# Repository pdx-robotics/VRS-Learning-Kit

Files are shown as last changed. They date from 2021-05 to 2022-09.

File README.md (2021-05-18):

This is a learning kit developed by Michael Nguyen. It is intended to train Viking Robotics
Society (VRS) students in the mechanical and electrical assembly of robots. This project was initially
Michael Nguyen's first entry to his professional portfolio, but the president at the time, Anthony
Bruno, suggested that it should be utilized as a learning kit for VRS students as well.
Video footage of the VRS Learning Kit in action is found in this link: https://www.youtube.com/watch?v=XiWULx6cqs4
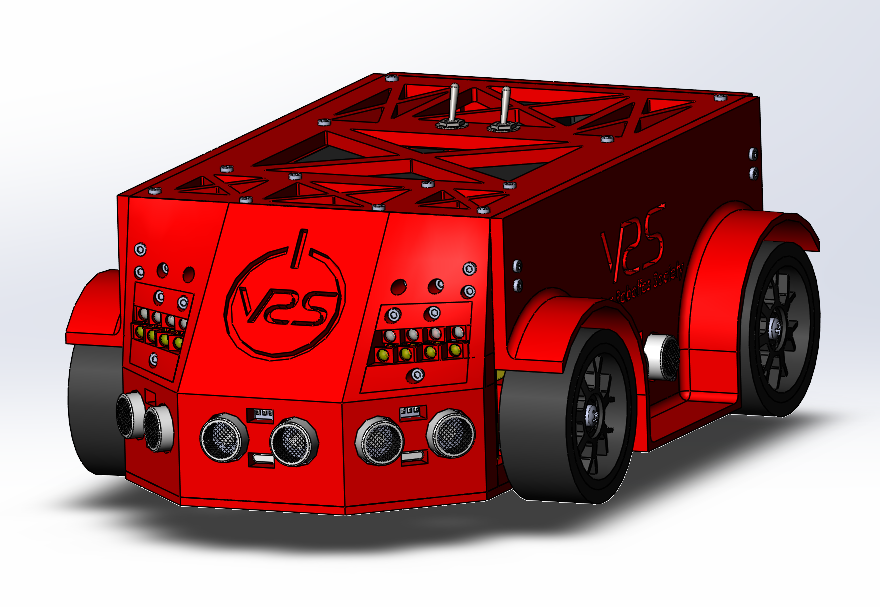
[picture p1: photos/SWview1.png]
 
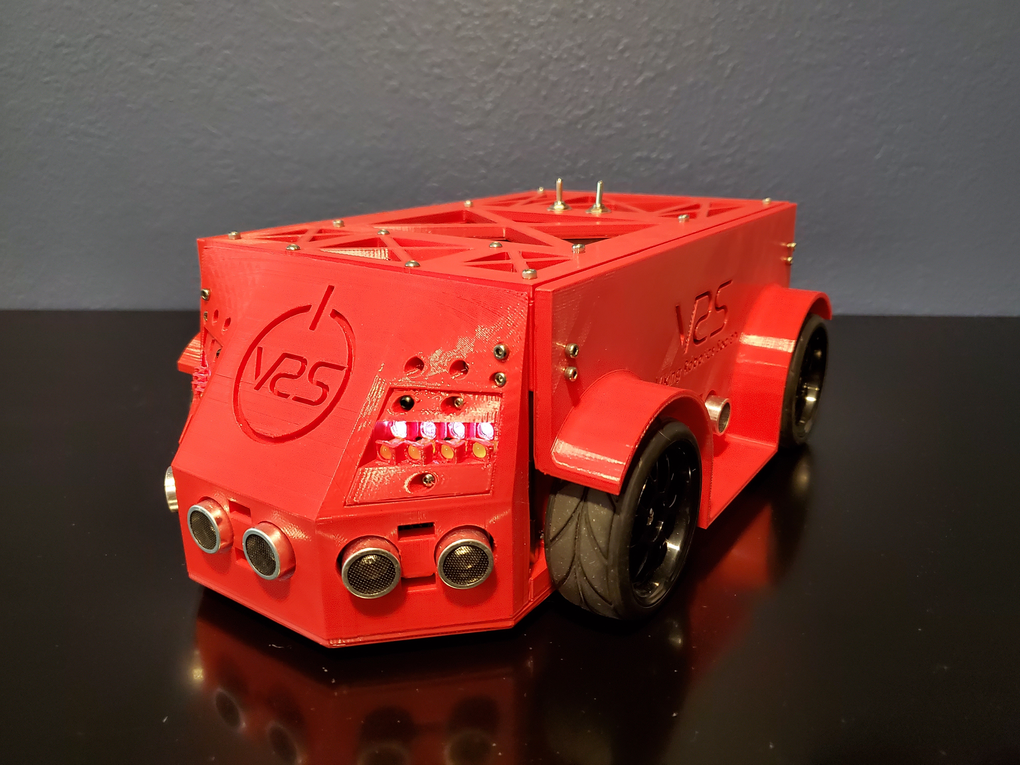
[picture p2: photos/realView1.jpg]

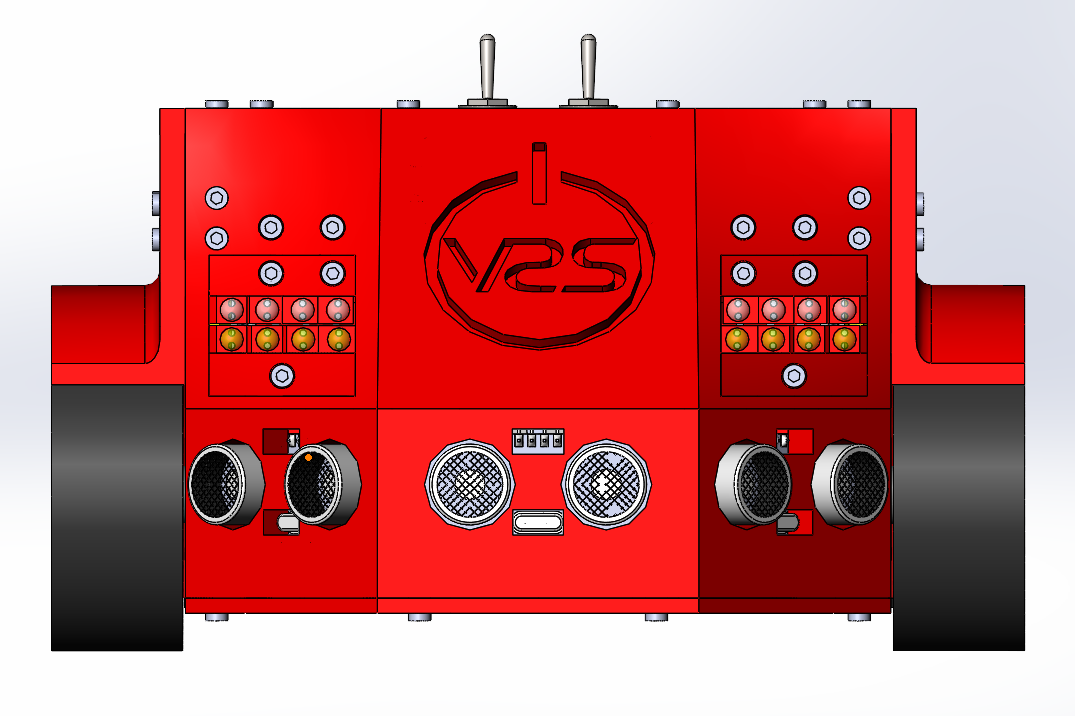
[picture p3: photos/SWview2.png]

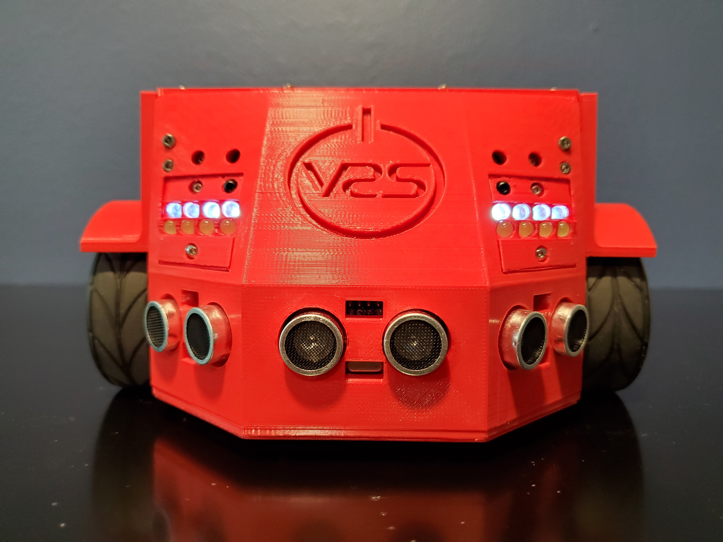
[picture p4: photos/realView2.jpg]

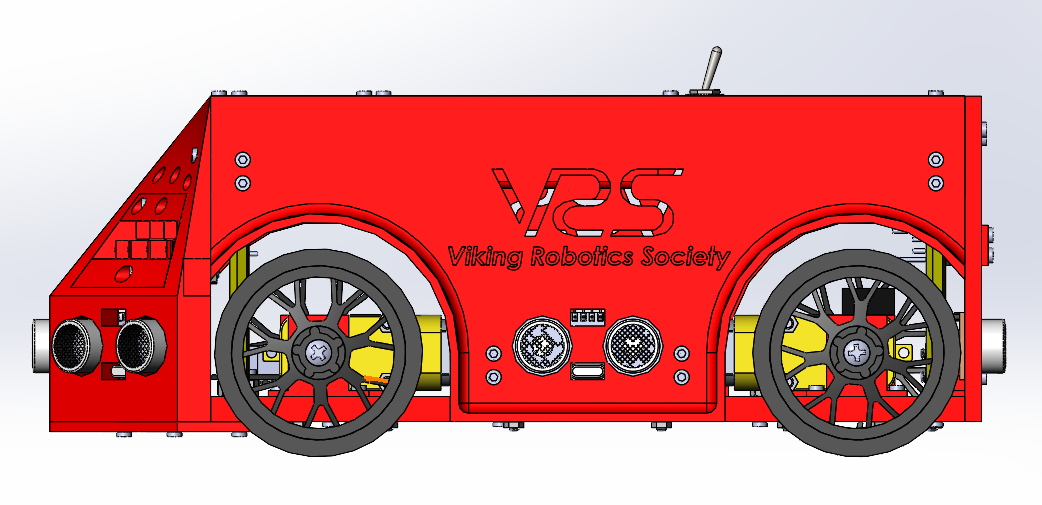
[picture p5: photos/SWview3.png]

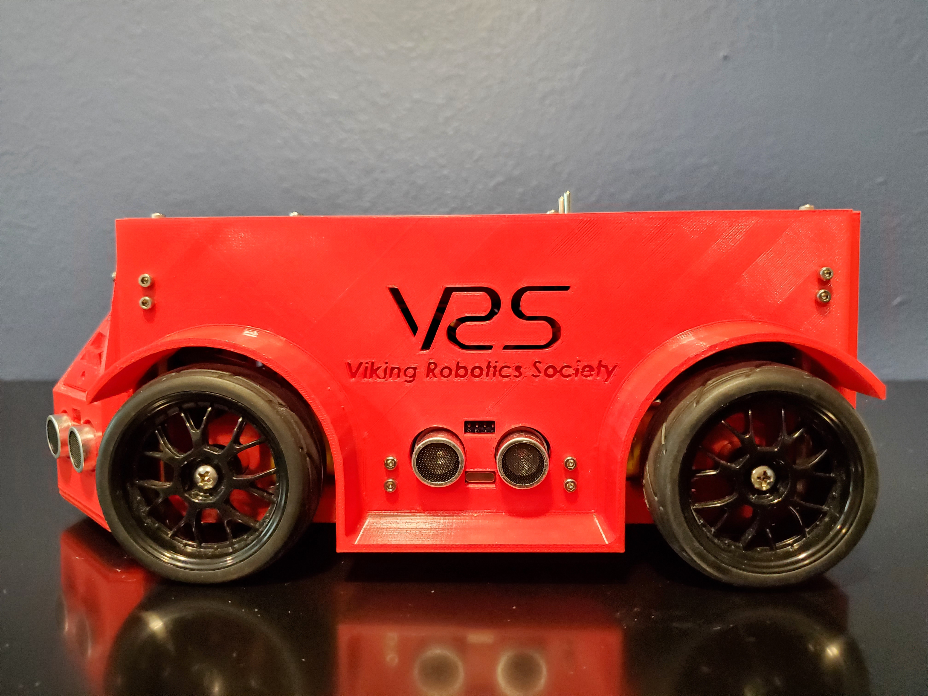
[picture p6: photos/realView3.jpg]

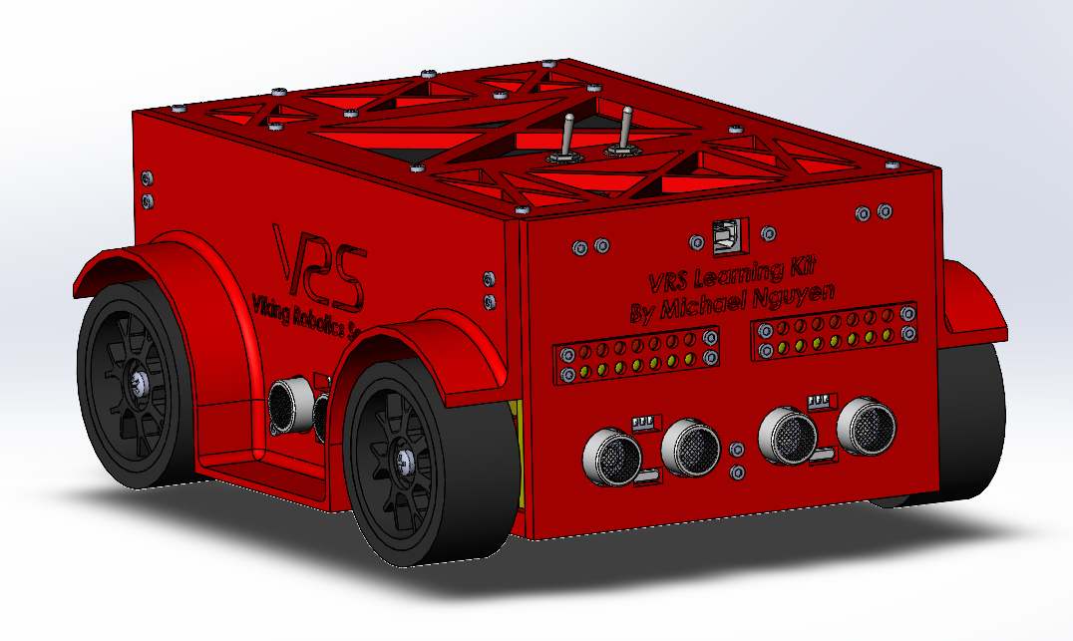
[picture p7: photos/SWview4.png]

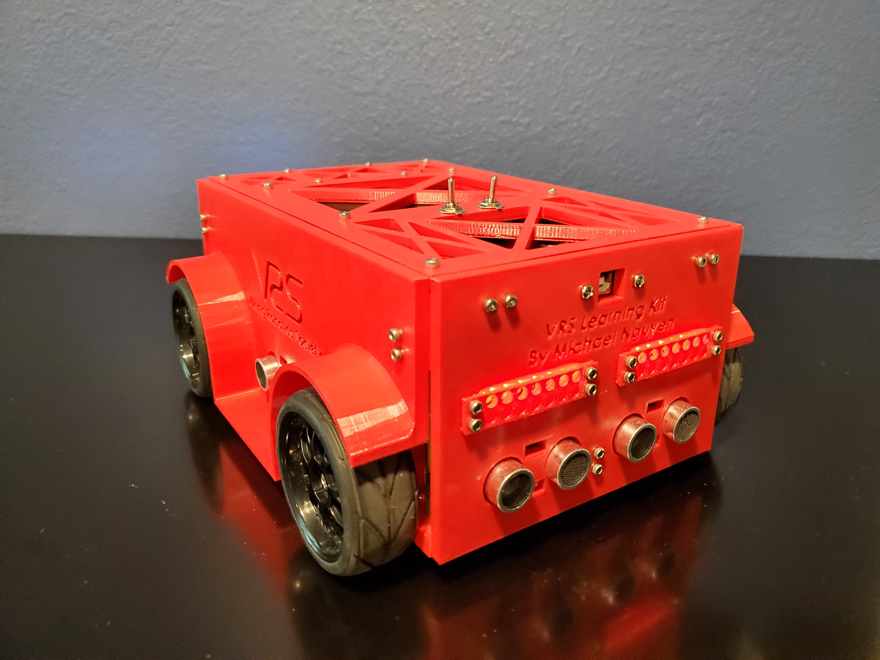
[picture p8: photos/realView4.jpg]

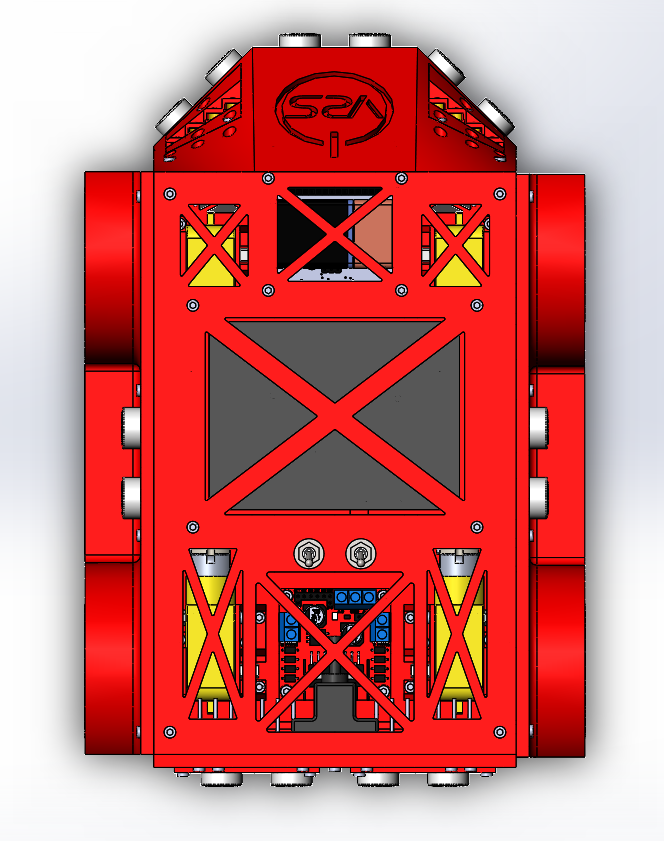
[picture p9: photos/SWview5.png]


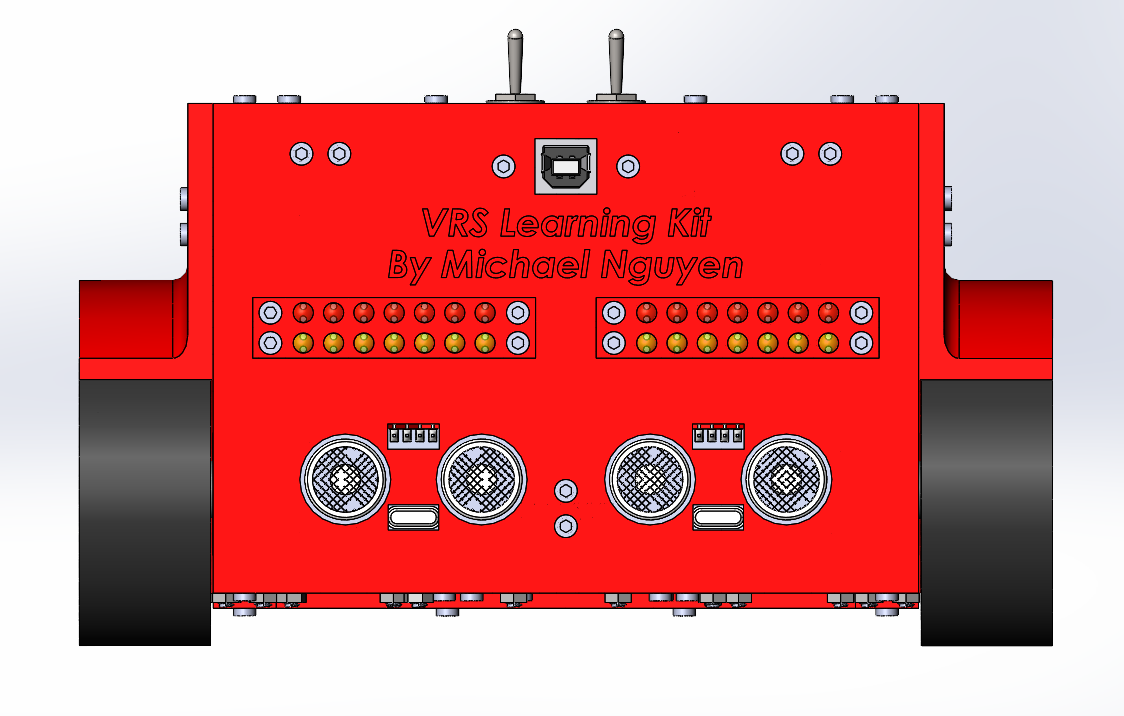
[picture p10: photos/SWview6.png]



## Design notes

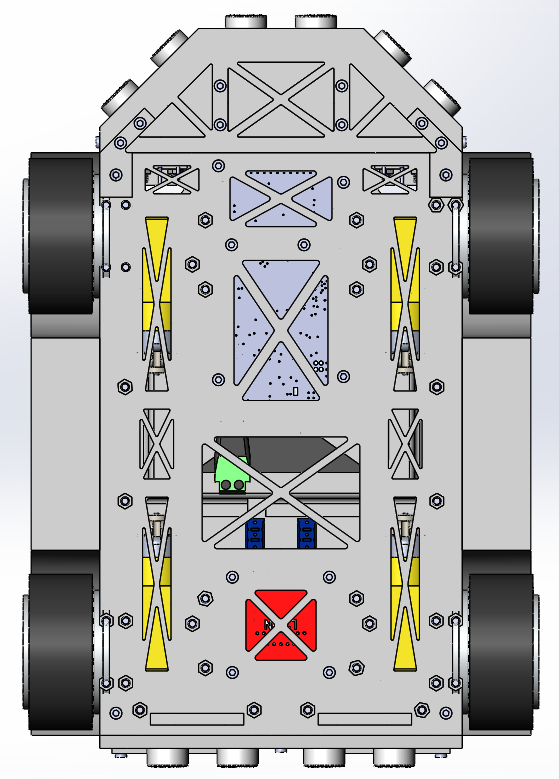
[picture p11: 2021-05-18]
photos/basicView4.png

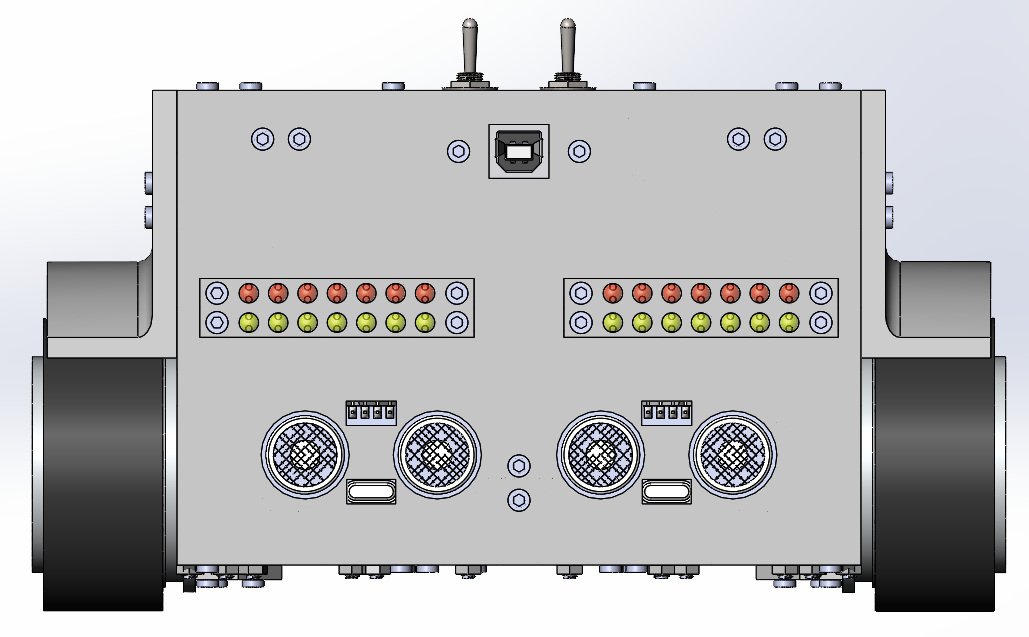
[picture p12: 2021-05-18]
photos/basicView3.png

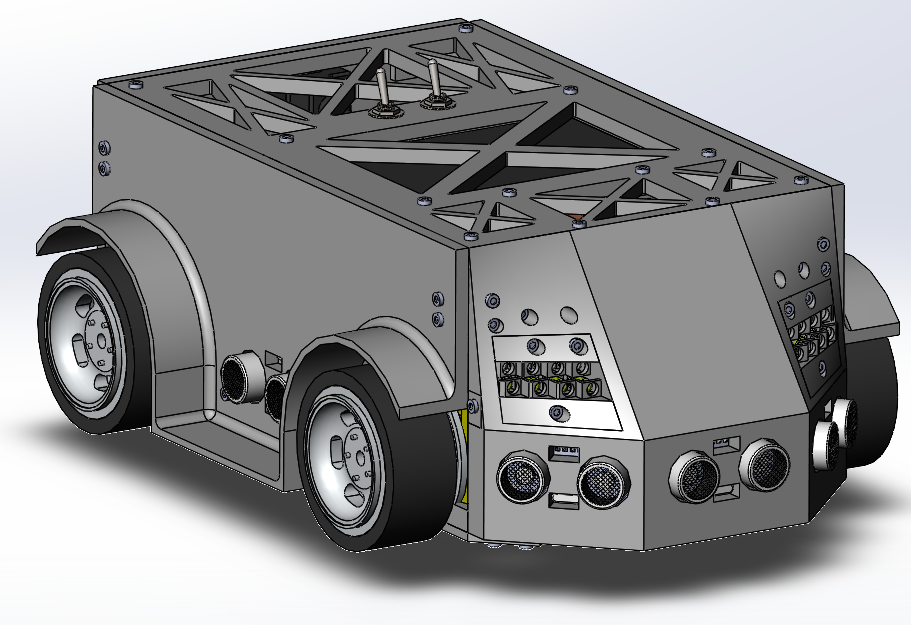
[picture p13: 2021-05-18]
photos/basicView1.png

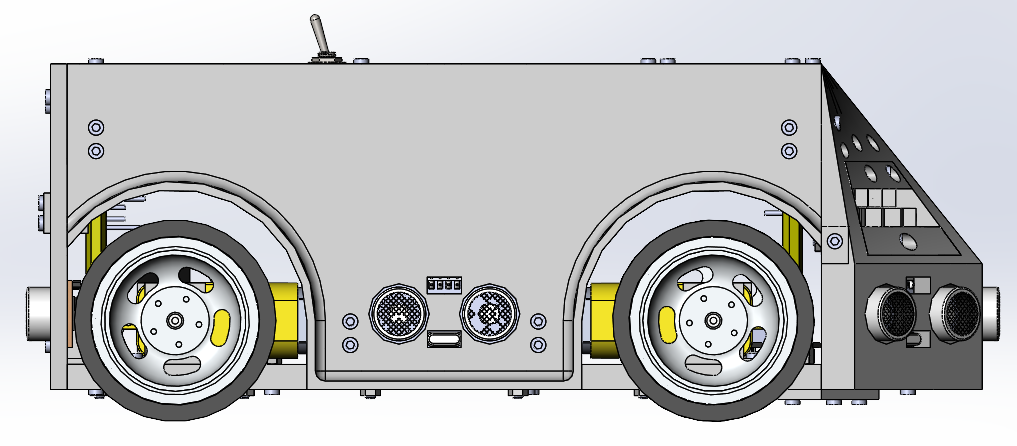
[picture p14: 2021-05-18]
photos/basicView6.png

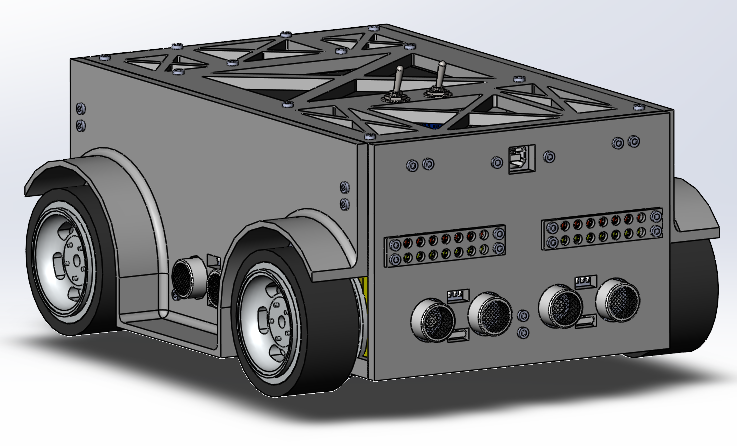
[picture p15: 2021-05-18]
photos/basicView7.png

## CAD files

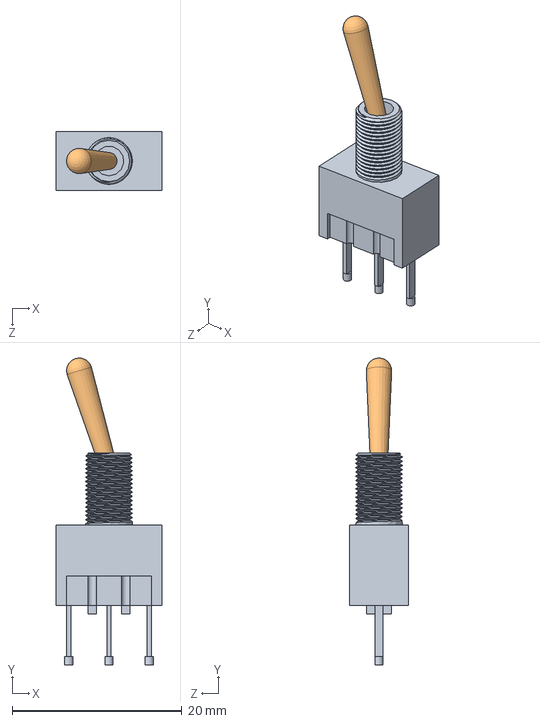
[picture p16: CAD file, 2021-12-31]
solidWorksParts/electronicComponents/toggleSwitch/toggle_mts1_assembly.SLDASM
12.5 x 36.2 x 7.00 mm
toggle_mts_1_base_thread
toggle_mts_1_lever

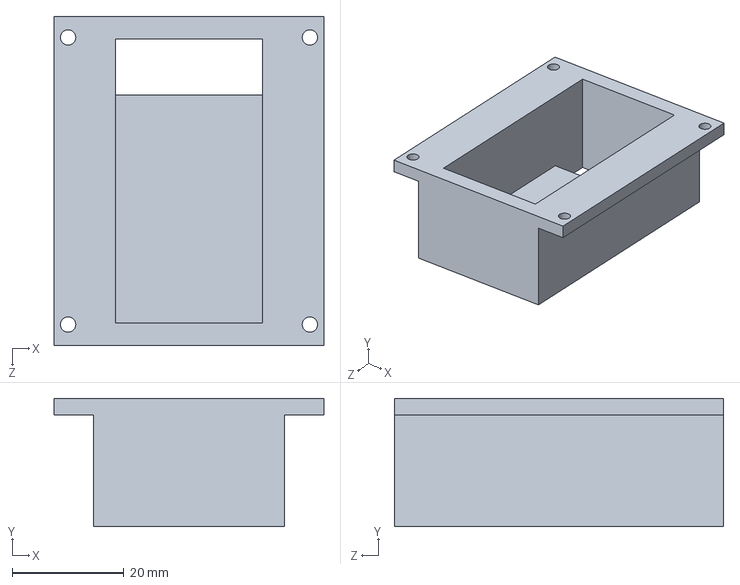
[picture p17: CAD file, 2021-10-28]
solidWorksParts/brackets/batteryBrackets/9VbatteryBracket/9VbatteryBracket.SLDPRT
48.2 x 23.0 x 58.8 mm

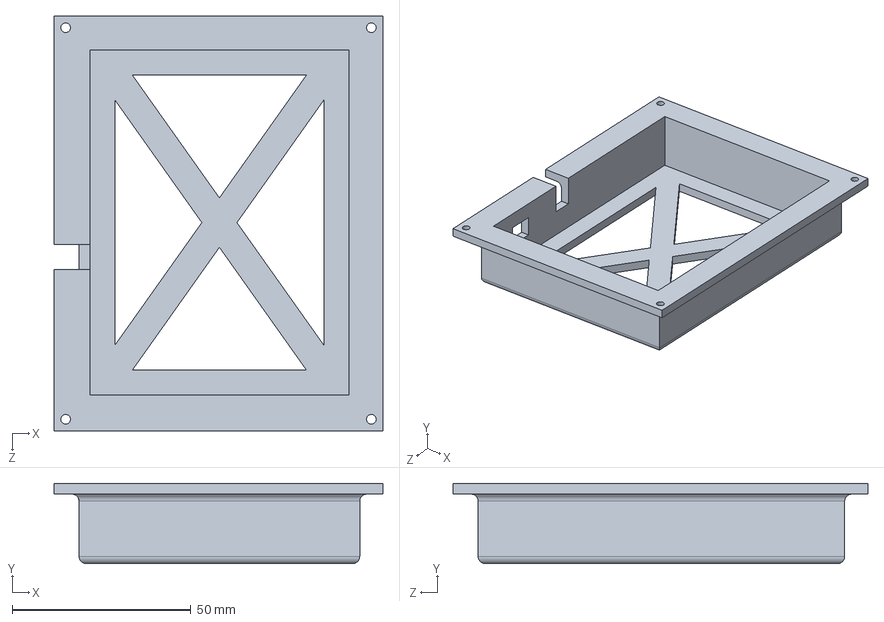
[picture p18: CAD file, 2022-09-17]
solidWorksParts/brackets/batteryBrackets/AAbatteryPackBracket/AAbatteryPackBracket.SLDPRT
92.0 x 22.5 x 116.0 mm

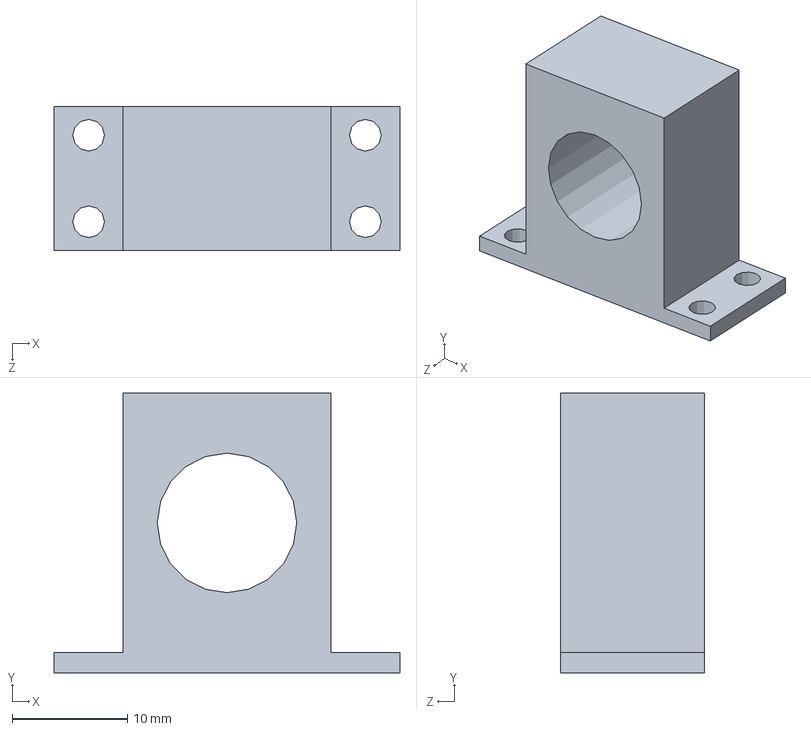
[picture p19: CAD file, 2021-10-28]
solidWorksParts/brackets/couplingCollarBracket/couplingCollarBracket.SLDPRT
30.0 x 24.2 x 12.5 mm

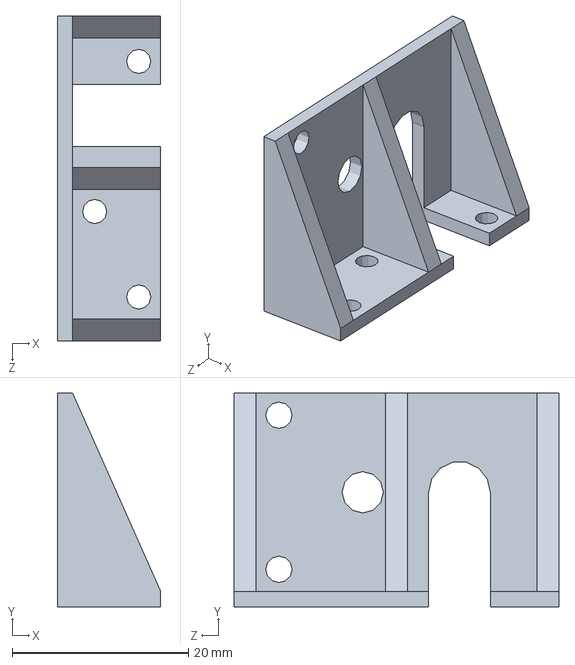
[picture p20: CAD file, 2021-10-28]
solidWorksParts/brackets/daguDCmotorBracket/daguDCmotorBracketPiece1/daguDCmotorBracketPiece1.SLDPRT
11.8 x 24.2 x 36.9 mm

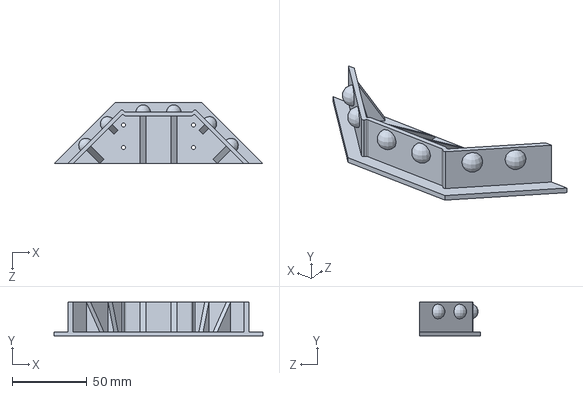
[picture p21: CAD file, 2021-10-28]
solidWorksParts/brackets/distanceSensorBrackets/frontDistanceSensorBracket/frontDistanceSensorBracket.SLDPRT
139.7 x 22.5 x 40.9 mm

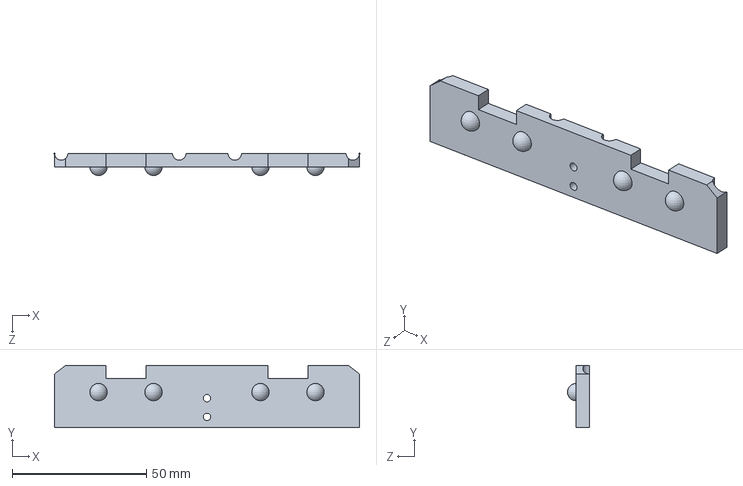
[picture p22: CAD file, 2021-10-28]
solidWorksParts/brackets/distanceSensorBrackets/rearDistanceSensorBracket/rearDistanceSensorBracket.SLDPRT
113.7 x 23.2 x 8.25 mm

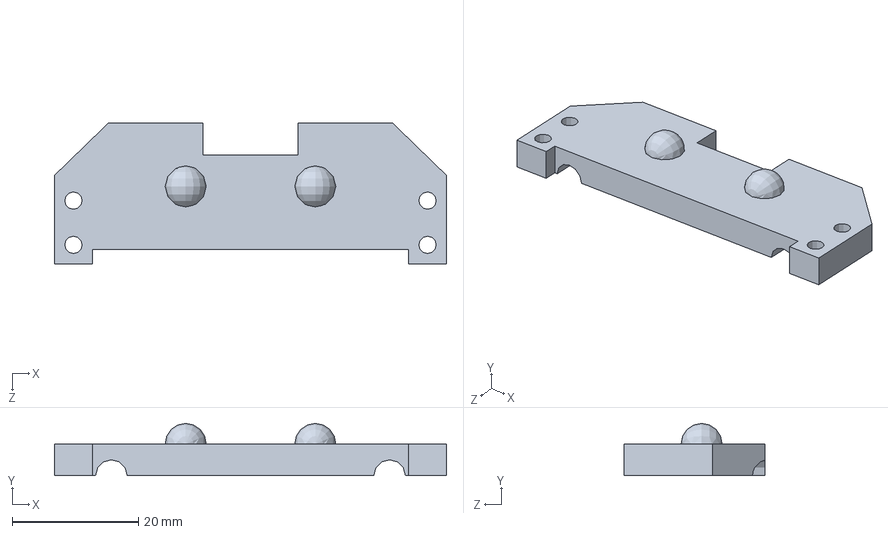
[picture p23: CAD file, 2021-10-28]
solidWorksParts/brackets/distanceSensorBrackets/sideDistanceSensorBracket/sideDistanceSensorBracket.SLDPRT
62.0 x 8.25 x 22.2 mm

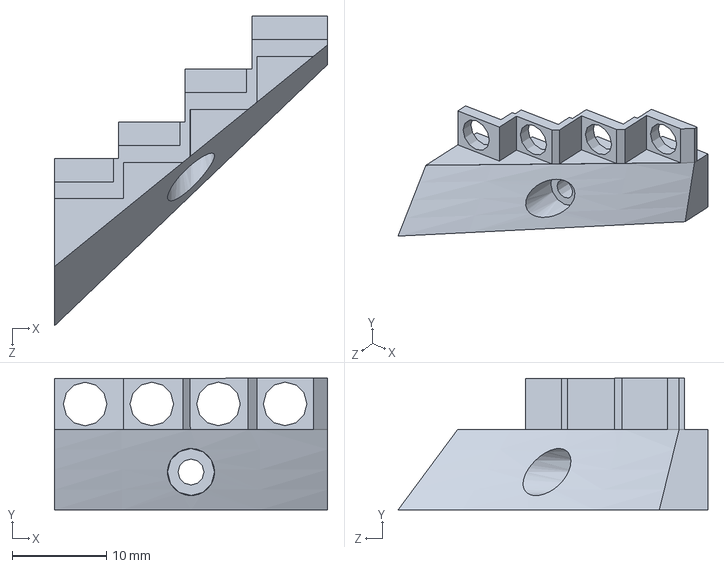
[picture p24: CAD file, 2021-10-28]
solidWorksParts/brackets/headLightBrackets/bottomHeadLights/bottomHeadLightLeft/bottomHeadLightLeftFront/bottomHeadLightLeftFront.SLDPRT
29.0 x 14.0 x 32.9 mm

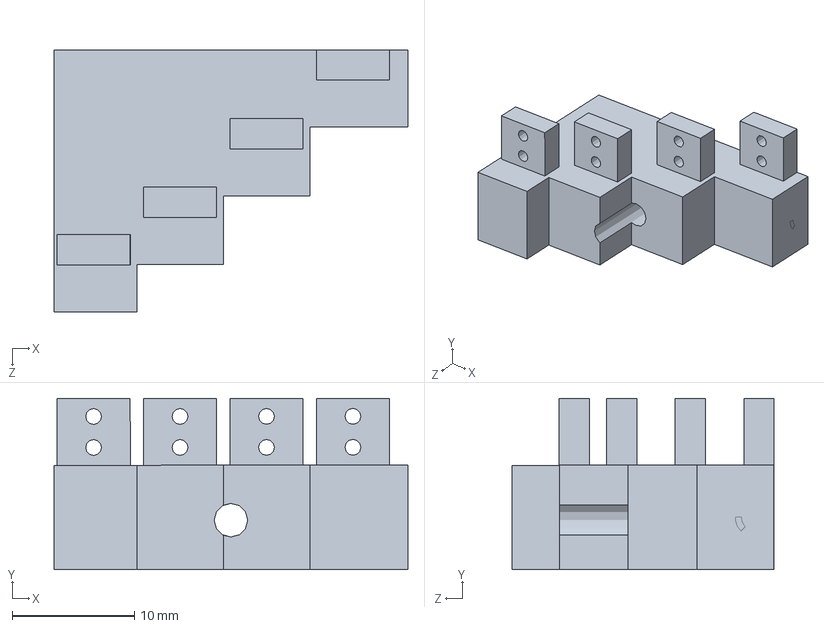
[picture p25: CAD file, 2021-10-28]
solidWorksParts/brackets/headLightBrackets/bottomHeadLights/bottomHeadLightLeft/bottomHeadLightLeftRear/bottomHeadLightLeftRear.SLDPRT
29.0 x 14.0 x 21.4 mm

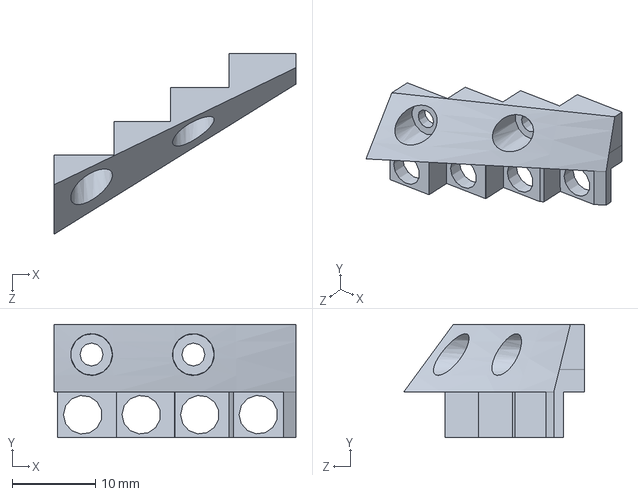
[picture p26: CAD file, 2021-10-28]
solidWorksParts/brackets/headLightBrackets/topHeadLights/topHeadLightLeft/topHeadLightLeftFront/topHeadLightLeftFront.SLDPRT
29.0 x 13.6 x 21.7 mm

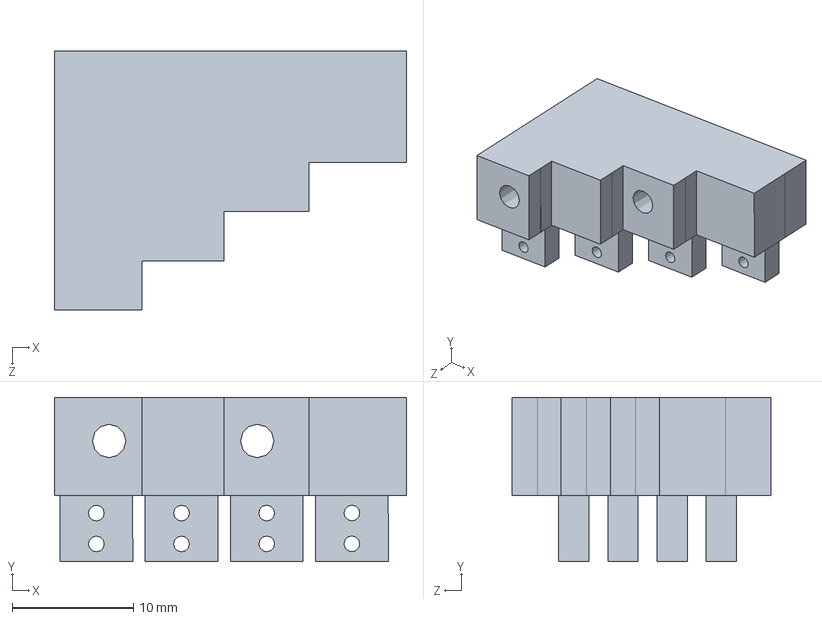
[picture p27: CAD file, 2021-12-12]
solidWorksParts/brackets/headLightBrackets/topHeadLights/topHeadLightLeft/topHeadLightLeftRear/topHeadLightLeftRear.SLDPRT
29.0 x 13.6 x 21.4 mm

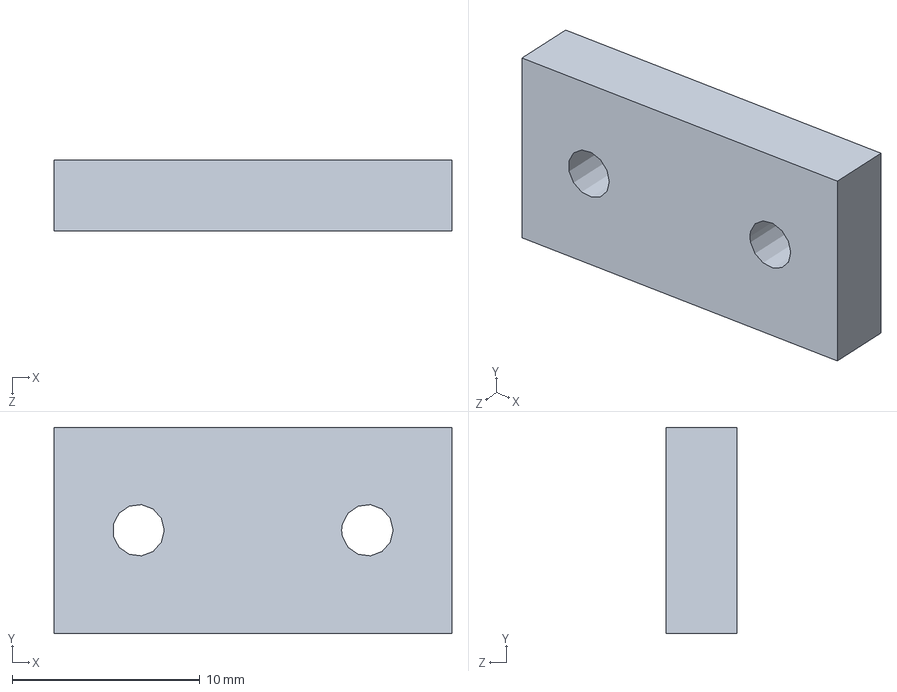
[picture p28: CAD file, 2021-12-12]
solidWorksParts/brackets/headLightBrackets/topHeadLights/topHeadLightSpacer/topHeadLightSpacer.SLDPRT
21.2 x 11.0 x 3.76 mm

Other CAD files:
solidWorksParts/brackets/daguDCmotorBracket/daguDCmotorBracketPiece2/daguDCmotorBracketPiece2.SLDPRT
solidWorksParts/brackets/headLightBrackets/bottomHeadLights/bottomHeadLightRight/bottomHeadLightRightFront/bottomHeadLightRightFront.SLDPRT
solidWorksParts/brackets/headLightBrackets/bottomHeadLights/bottomHeadLightRight/bottomHeadLightRightRear/bottomHeadLightRightRear.SLDPRT
solidWorksParts/brackets/headLightBrackets/topHeadLights/topHeadLightRight/topHeadLightRightFront/topHeadLightRightFront.SLDPRT
solidWorksParts/brackets/headLightBrackets/topHeadLights/topHeadLightRight/topHeadLightRightRear/topHeadLightRightRear.SLDPRT
solidWorksDrawings/brackets/batteryBrackets/9VbatteryBracket/9VbatteryBracket.SLDDRW
solidWorksDrawings/brackets/batteryBrackets/AAbatteryPackBracket/AAbatteryPackBracket.SLDDRW
solidWorksDrawings/brackets/couplingCollarBracket/couplingCollarBracket.SLDDRW
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

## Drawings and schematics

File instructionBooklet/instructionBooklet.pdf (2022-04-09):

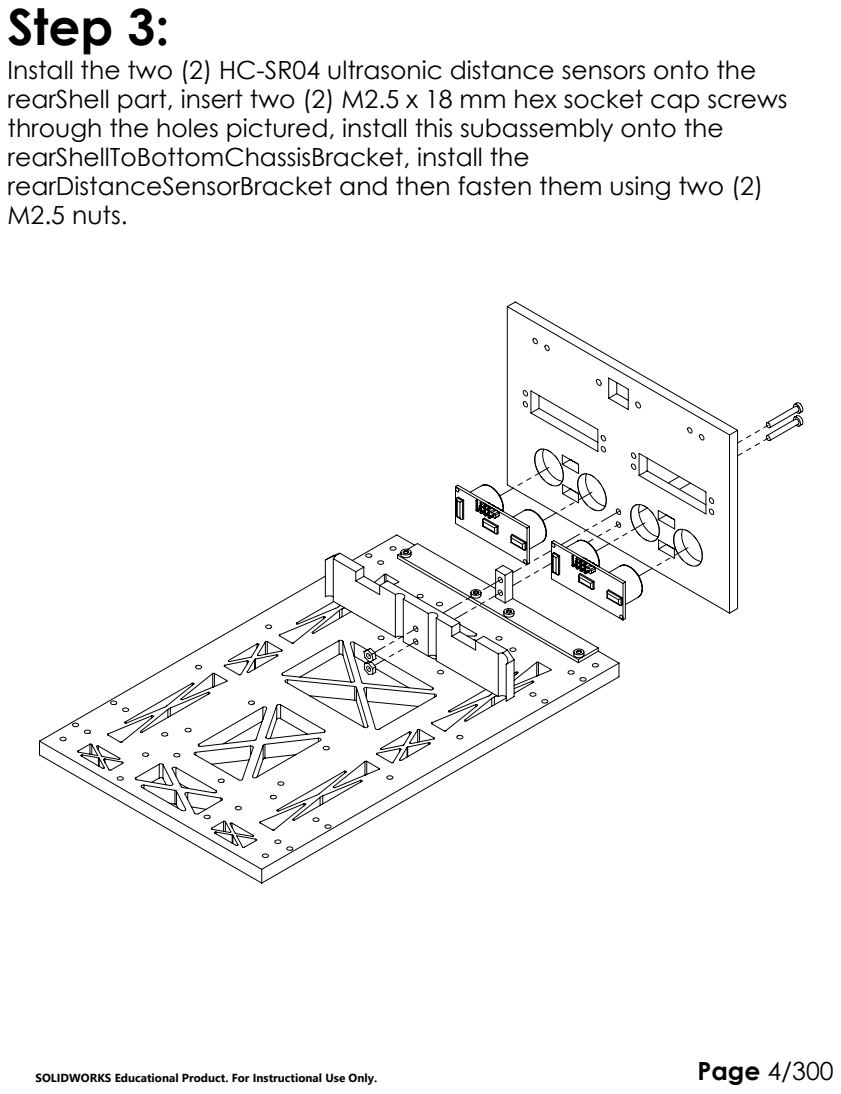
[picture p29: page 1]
SOLIDWORKS Educational Product. For Instructional Use Only.; Page 4/300

Step 3:
Install the two (2) HC-SR04 ultrasonic distance sensors onto the
rearShell part, insert two (2) M2.5 x 18 mm hex socket cap screws
through the holes pictured, install this subassembly onto the
rearShellToBottomChassisBracket, install the
rearDistanceSensorBracket and then fasten them using two (2)
M2.5 nuts.

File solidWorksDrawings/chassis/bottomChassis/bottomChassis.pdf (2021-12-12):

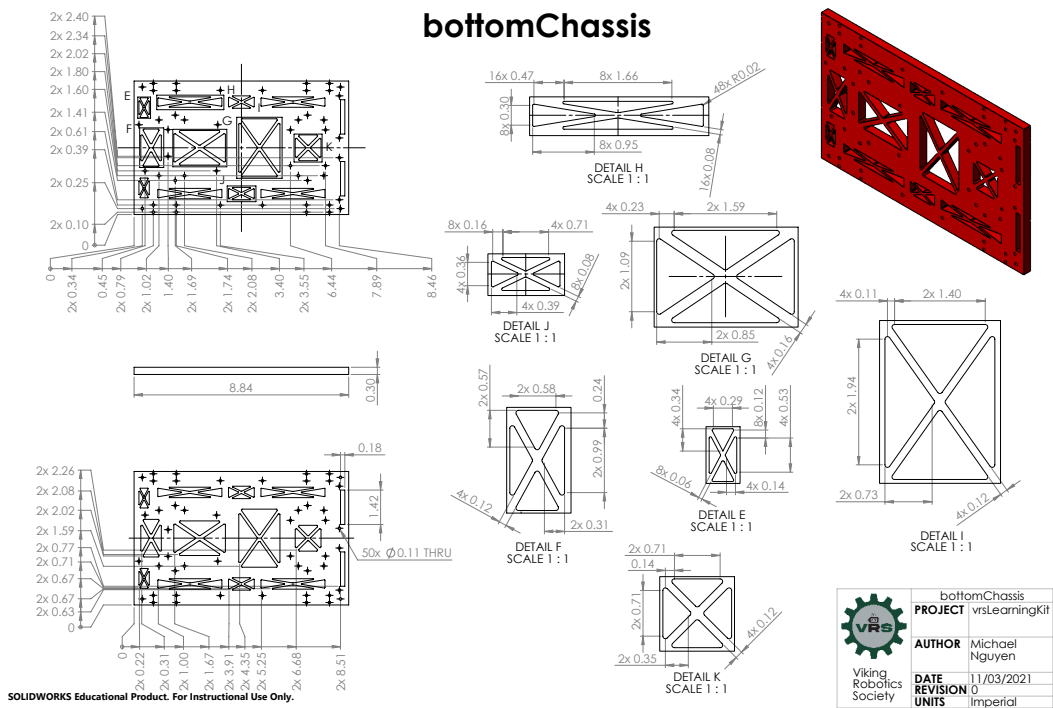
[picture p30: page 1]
DETAIL E SCALE 1 : 1; DETAIL F SCALE 1 : 1; DETAIL G SCALE 1 : 1; DETAIL H SCALE 1 : 1; DETAIL I SCALE 1 : 1; DETAIL J SCALE 1 : 1; DETAIL K SCALE 1 : 1; 50x 0.11 THRU; SOLIDWORKS Educational Product. For Instructional Use Only.; Society

Viking Robotics | bottomChassis

PROJECT | vrsLearningKit

AUTHOR | Michael Nguyen

DATE | 11/03/2021
REVISION | 0
UNITS | Imperial

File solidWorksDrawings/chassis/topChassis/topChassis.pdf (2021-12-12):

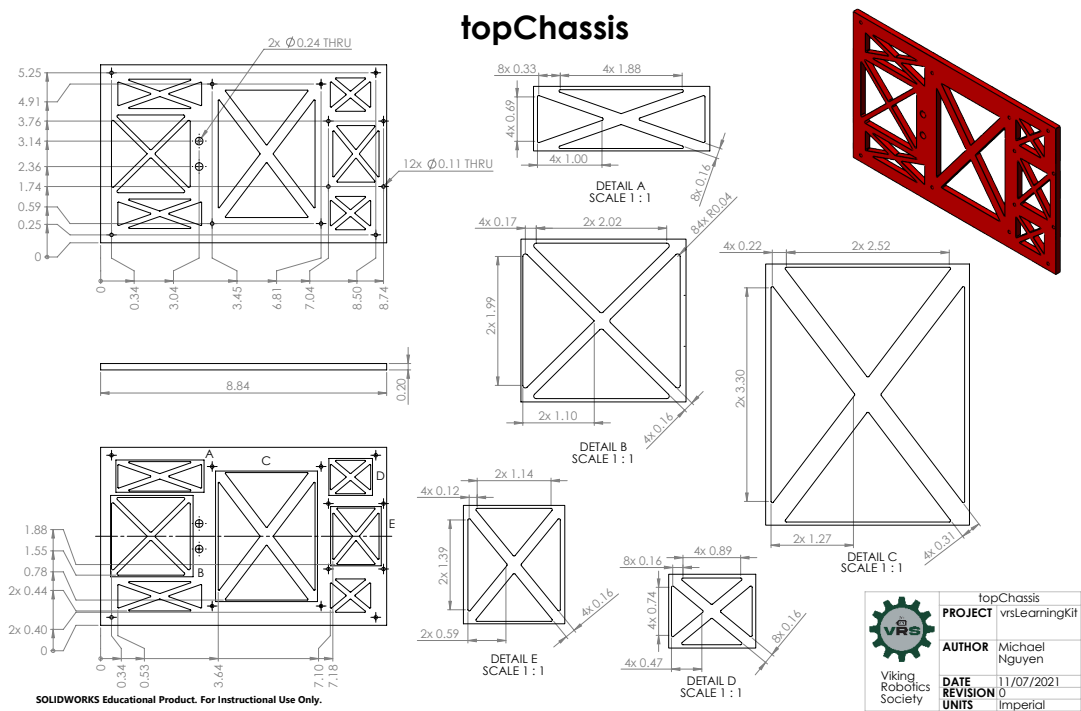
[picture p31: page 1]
12x 0.11 THRU; 2x 0.24 THRU; DETAIL A SCALE 1 : 1; DETAIL B SCALE 1 : 1; DETAIL C SCALE 1 : 1; DETAIL D SCALE 1 : 1; DETAIL E SCALE 1 : 1; SOLIDWORKS Educational Product. For Instructional Use Only.; Society

Viking Robotics | topChassis

PROJECT | vrsLearningKit

AUTHOR | Michael Nguyen

DATE | 11/07/2021
REVISION | 0
UNITS | Imperial

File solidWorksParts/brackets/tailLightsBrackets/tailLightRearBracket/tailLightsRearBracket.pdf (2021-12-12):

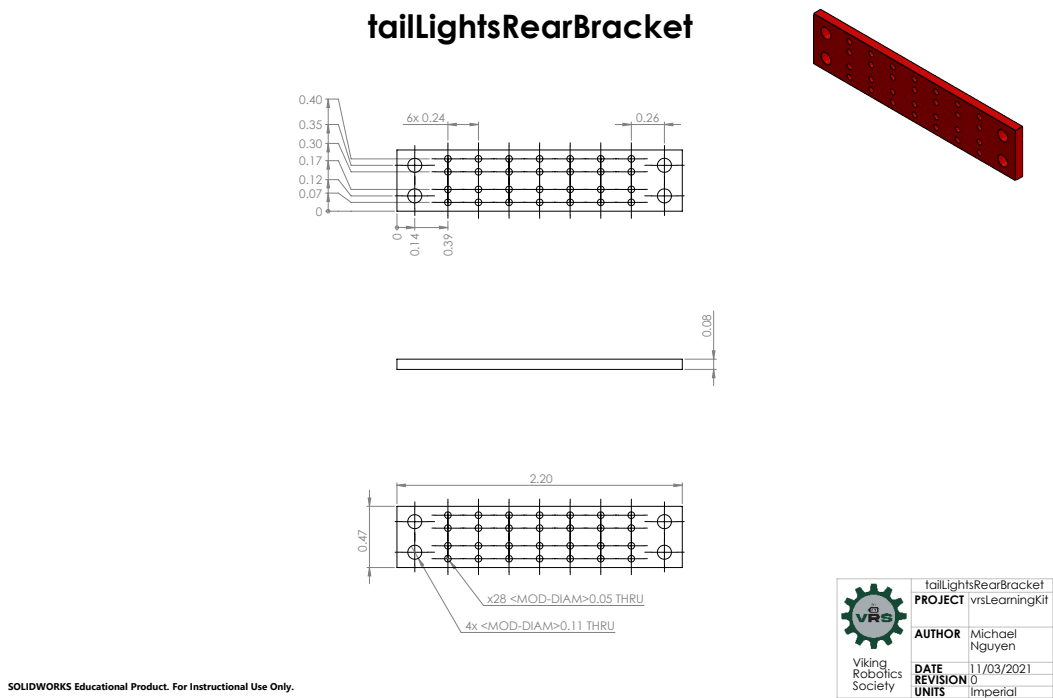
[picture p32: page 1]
SOLIDWORKS Educational Product. For Instructional Use Only.; Society

Viking Robotics | tailLightsRearBracket

x28 <MOD-DIAM>0.05 THRU
4x <MOD-DIAM>0.11 THRU

PROJECT | vrsLearningKit

AUTHOR | Michael Nguyen

DATE | 11/03/2021
REVISION | 0
UNITS | Imperial

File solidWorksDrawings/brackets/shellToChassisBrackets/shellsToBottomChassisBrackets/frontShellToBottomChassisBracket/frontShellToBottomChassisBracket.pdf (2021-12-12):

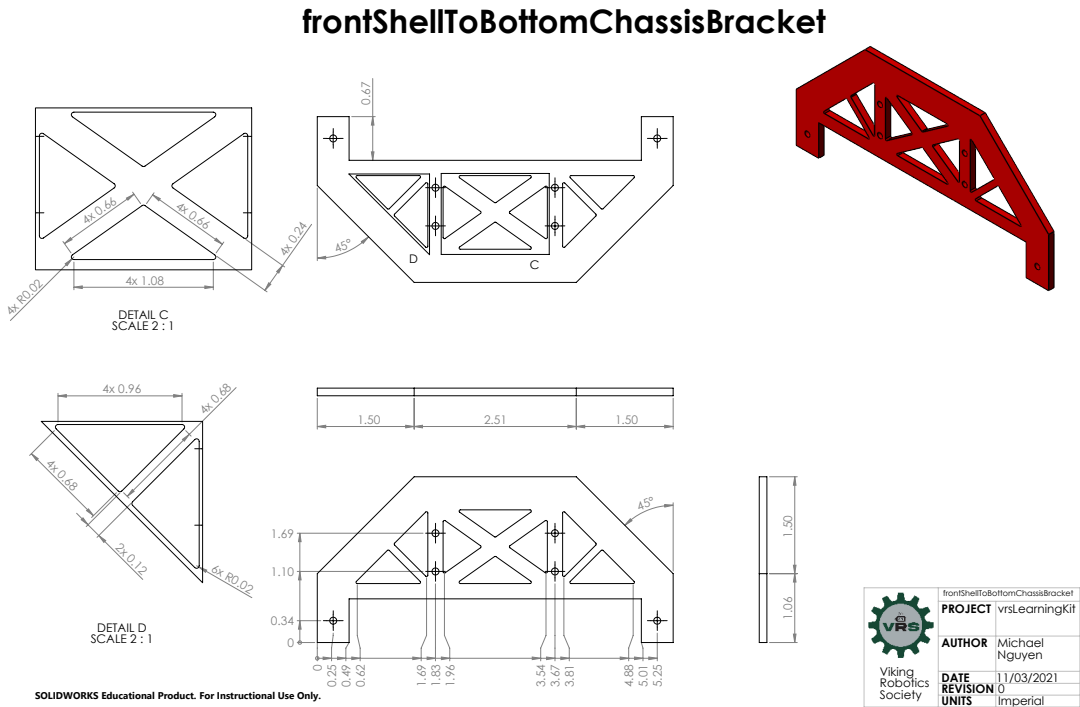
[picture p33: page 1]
DETAIL C SCALE 2 : 1; DETAIL D SCALE 2 : 1; SOLIDWORKS Educational Product. For Instructional Use Only.; Society

Viking Robotics | frontShellToBottomChassisBracket

PROJECT | vrsLearningKit

AUTHOR | Michael Nguyen

DATE | 11/03/2021
REVISION | 0
UNITS | Imperial

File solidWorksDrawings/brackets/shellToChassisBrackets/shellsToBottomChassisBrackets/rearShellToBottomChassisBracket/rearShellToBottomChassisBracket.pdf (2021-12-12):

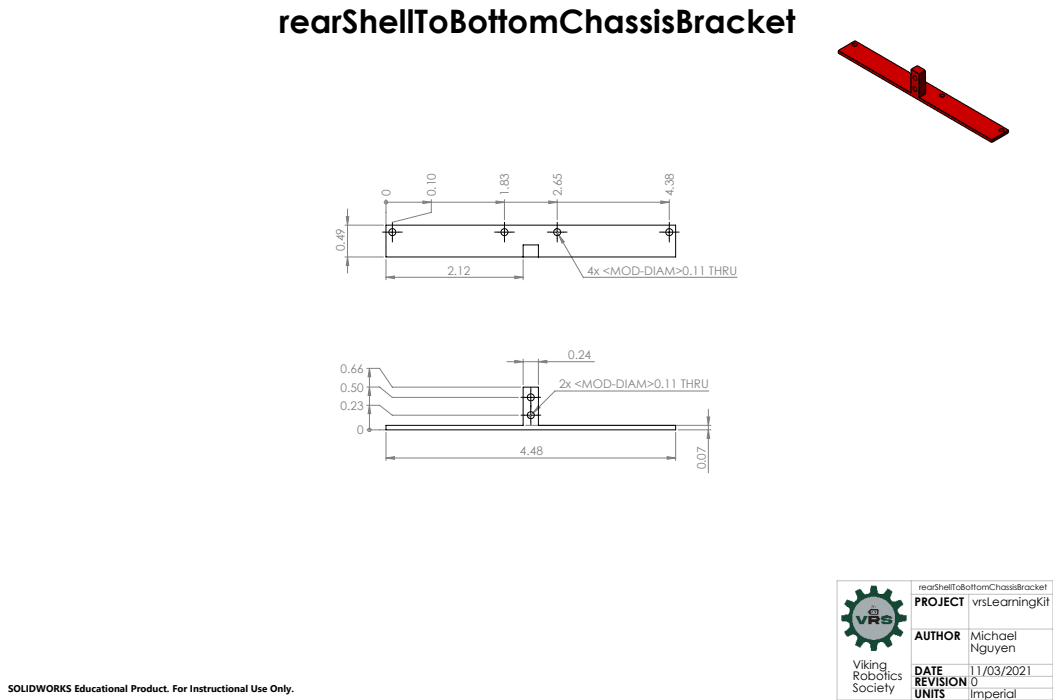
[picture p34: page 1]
SOLIDWORKS Educational Product. For Instructional Use Only.; Society

4x <MOD-DIAM>0.11 THRU

2x <MOD-DIAM>0.11 THRU

Viking Robotics | rearShellToBottomChassisBracket

PROJECT | vrsLearningKit

AUTHOR | Michael Nguyen

DATE | 11/03/2021
REVISION | 0
UNITS | Imperial

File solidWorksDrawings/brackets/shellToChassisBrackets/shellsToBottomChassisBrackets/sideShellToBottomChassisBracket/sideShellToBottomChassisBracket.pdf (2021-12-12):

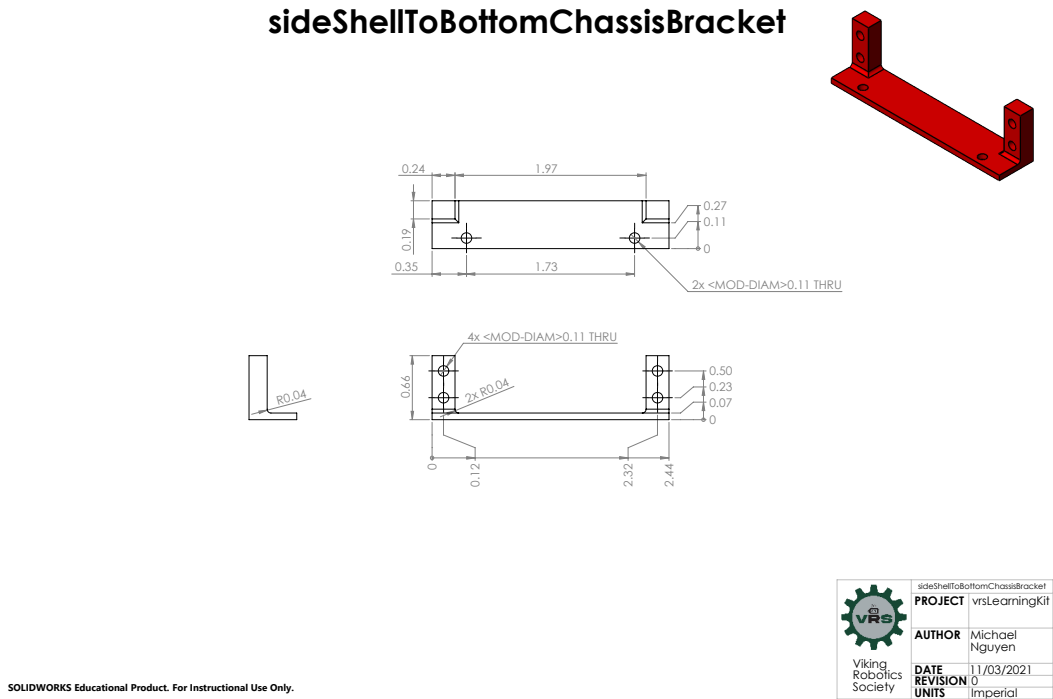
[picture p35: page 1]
SOLIDWORKS Educational Product. For Instructional Use Only.; Society

2x <MOD-DIAM>0.11 THRU

4x <MOD-DIAM>0.11 THRU

Viking Robotics | sideShellToBottomChassisBracket

PROJECT | vrsLearningKit

AUTHOR | Michael Nguyen

DATE | 11/03/2021
REVISION | 0
UNITS | Imperial

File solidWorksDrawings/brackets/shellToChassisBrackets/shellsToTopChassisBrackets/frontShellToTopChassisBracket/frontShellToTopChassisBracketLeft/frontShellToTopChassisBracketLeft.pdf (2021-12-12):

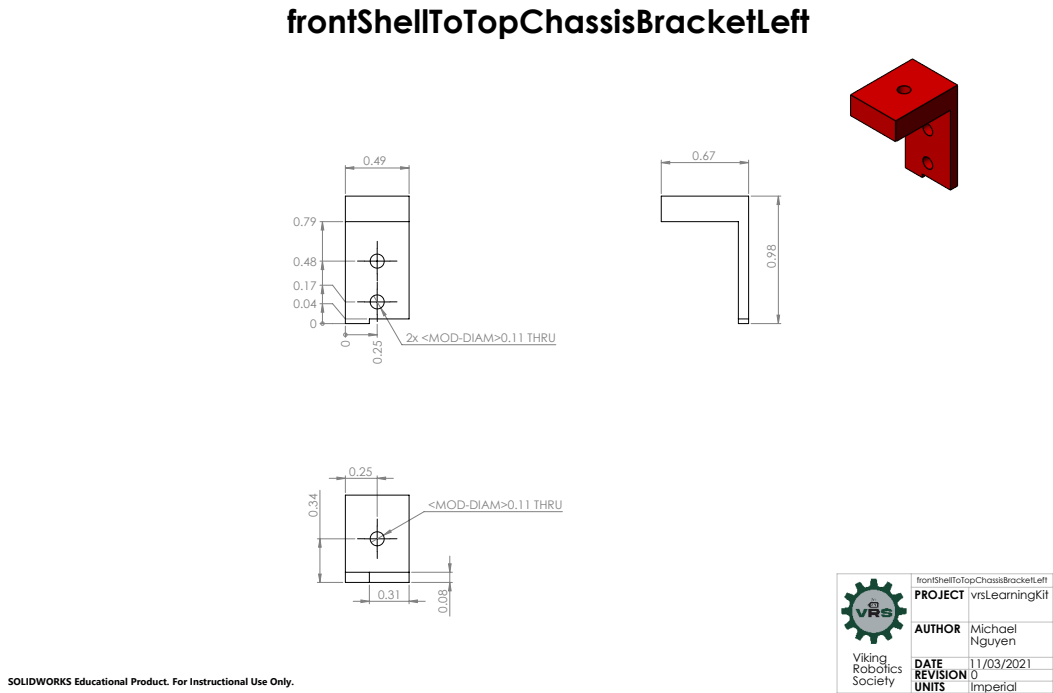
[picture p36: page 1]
SOLIDWORKS Educational Product. For Instructional Use Only.; Society

2x <MOD-DIAM>0.11 THRU

<MOD-DIAM>0.11 THRU

Viking Robotics | frontShellToTopChassisBracketLeft

PROJECT | vrsLearningKit

AUTHOR | Michael Nguyen

DATE | 11/03/2021
REVISION | 0
UNITS | Imperial

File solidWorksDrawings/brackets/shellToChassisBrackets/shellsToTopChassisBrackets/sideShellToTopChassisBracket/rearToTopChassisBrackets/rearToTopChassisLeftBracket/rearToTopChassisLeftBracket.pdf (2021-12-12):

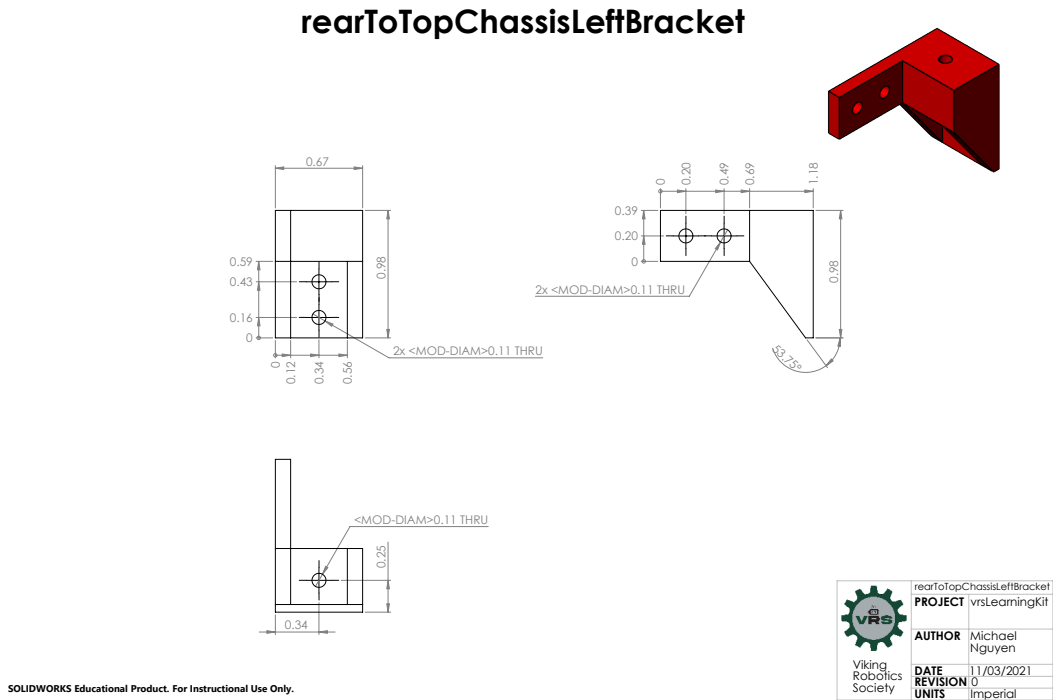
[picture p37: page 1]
2x <MOD-DIAM>0.11 THRU 0; SOLIDWORKS Educational Product. For Instructional Use Only.; Society

2x <MOD-DIAM>0.11 THRU

<MOD-DIAM>0.11 THRU 0.25

Viking Robotics | rearToTopChassisLeftBracket

PROJECT | vrsLearningKit

AUTHOR | Michael Nguyen

DATE | 11/03/2021
REVISION | 0
UNITS | Imperial

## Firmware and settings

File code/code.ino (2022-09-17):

// Motor A setup

  int enableMotorA = 22; // Enables PWM signal for Motor A.
  int motorAdirection1 = 24; // Spinning direction of motor A [IN2] (i).
  int motorAdirection2 = 23; // Spinning direction of motor A [IN1] (ii).


// Motor B setup

  int enableMotorB = 27; //Enables PWM signal for Motor B.
  int motorBdirection1 = 25; // Spinning direction of motor B [IN4] (i).
  int motorBdirection2 = 26; // Spinning direction of motor B [IN3] (ii).


// Left turn signal setup

  int frontLeftTurnSignal = 7;
  int rearLeftTurnSignal = 50;


// Right turn signal setup

  int frontRightTurnSignal = 30;
  int rearRightTurnSignal = 47;

// Distance sensor setup

  // Front center distance sensor
  
    #define trigPinFC 31
    #define echoPinFC 32
    
  // Front left distance sensor
  
    #define trigPinFL 34 
    #define echoPinFL 35 
    
  // Front right distance sensor

    #define trigPinFR 6 
    #define echoPinFR 5 
  
  // Left side skirt distance sensor

    #define trigPinLSS 11
    #define echoPinLSS 10
  
  // Right side skirt distance sensor

    #define trigPinRSS 50
    #define echoPinRSS 51
  
  // Rear left distance sensor

    #define trigPinRL 12
    #define echoPinRL 13
  
  // Rear right distance sensor

    #define trigPinRR 48
    #define echoPinRR 49


void setup() {

  // Configure motor A:
  
    pinMode(enableMotorA, OUTPUT);
    pinMode(motorAdirection1, OUTPUT);
    pinMode(motorAdirection2, OUTPUT);


  // Configure motor B:
  
    pinMode(enableMotorB, OUTPUT);
    pinMode(motorBdirection1, OUTPUT);
    pinMode(motorBdirection2, OUTPUT);


  // Configure distance sensors:

    // Front center distance sensor

      pinMode(trigPinFC, OUTPUT);
      pinMode(echoPinFC, INPUT);

    // Front left distance sensor

      pinMode(trigPinFL, OUTPUT);
      pinMode(echoPinFL, INPUT);

    // Front right distance sensor

      pinMode(trigPinFR, OUTPUT);
      pinMode(echoPinFR, INPUT);

    // Left side skirt distance sensor

      pinMode(trigPinLSS, OUTPUT);
      pinMode(echoPinLSS, INPUT);
      
    // Right side skirt distance sensor

      pinMode(trigPinRSS, OUTPUT);
      pinMode(echoPinRSS, INPUT);

    // Rear left distance sensor

      pinMode(trigPinRL, OUTPUT);
      pinMode(echoPinRL, INPUT);

    // Rear right distance sensor

      pinMode(trigPinRR, OUTPUT);
      pinMode(echoPinRR, INPUT);

  // Configure turn signals:

    // Left turn signal

      pinMode(frontLeftTurnSignal, OUTPUT);
      pinMode(rearLeftTurnSignal, OUTPUT);

    // Right turn signal

      pinMode(frontRightTurnSignal, OUTPUT);
      pinMode(rearRightTurnSignal, OUTPUT);

  }


void loop() {
  movement();
  avoid();
  }


// Motor functions

  void forwardMotorA(){
    // Turns motor A on in the forward direction.
    digitalWrite(motorAdirection1, HIGH);
    digitalWrite(motorAdirection2, LOW);
  }


  void forwardMotorB(){
    // Turns motor B on in the forward direction.
    digitalWrite(motorBdirection1, LOW);
    digitalWrite(motorBdirection2, HIGH);
  }


  void backwardMotorA(){
    // Turns motor A on in the backward direction.
    digitalWrite(motorAdirection1, LOW);
    digitalWrite(motorAdirection2, HIGH);
  }


  void backwardMotorB(){
    // Turns motor B on in the backward direction.
    digitalWrite(motorBdirection1, HIGH);
    digitalWrite(motorBdirection2, LOW);
  }


  void stopMotorA(){
    // Motor A's shaft stops rotating.
    digitalWrite(motorAdirection1, HIGH);
    digitalWrite(motorAdirection2, HIGH);
  }


  void stopMotorB(){
    // Motor B's shaft stops rotating.
    digitalWrite(motorBdirection1, HIGH);
    digitalWrite(motorBdirection2, HIGH);
  }


  void coastMotorA(){
    // Car will coast from forward momentum from power of Motor A before it was turned off.
    digitalWrite(motorAdirection1, LOW);
    digitalWrite(motorAdirection2, LOW);
  }


  void coastMotorB(){
    // Car will coast from forward momentum from power of Motor B before it was turned off.
    digitalWrite(motorBdirection1, LOW);
    digitalWrite(motorBdirection2, LOW);
  }


  void motorAon(){
    // Turns motor A on.
    digitalWrite(enableMotorA, HIGH);
  }


  void motorBon(){
    // Turns motor B on.
    digitalWrite(enableMotorB, HIGH);
  }


  void motorAoff(){
    // Turns motor A off.
    digitalWrite(enableMotorA, LOW);
  }


  void motorBoff(){
    // Turns motor B off.
    digitalWrite(enableMotorB, LOW);
  }


// Movement functions

  void forward(int duration){
    // Car will move forward.
    forwardMotorA();
    forwardMotorB();
    delay(duration);
  }


  void backward(int duration){
    // Car will move backward.
    digitalWrite(frontLeftTurnSignal, HIGH);
    digitalWrite(rearLeftTurnSignal, HIGH);
    digitalWrite(frontRightTurnSignal, HIGH);
    digitalWrite(rearRightTurnSignal, HIGH);
    delay(100);
    digitalWrite(frontLeftTurnSignal, LOW);
    digitalWrite(rearLeftTurnSignal, LOW);
    digitalWrite(frontRightTurnSignal, LOW);
    digitalWrite(rearRightTurnSignal, LOW);
    delay(100);
    backwardMotorA();
    backwardMotorB();
    delay(duration);
  }


  void right(int duration){
    // Car will turn right.
    rightTurnSignal();
    backwardMotorA();
    forwardMotorB();
    delay(duration);
  }


  void left(int duration){
    // Car will turn left.
    leftTurnSignal();
    forwardMotorA();
    backwardMotorB();
    delay(duration);
  }


  void coast(int duration){
    // Car will coast.
    coastMotorA();
    coastMotorB();
    delay(duration);
  }


  void stopCar(int duration){
    // Car will stop.
    stopMotorA();
    stopMotorB();
    delay(duration);
  }


  void motorsOff(){
    // Both motors are turned off.
    motorAoff();
    motorBoff();
  }


  void motorsOn(){
    // Both motors are turned on.
    motorAon();
    motorBon();
  }


// Distance sensor measurements:

  // Front center distance sensor measurement
  
    int distanceFC(){
      int duration, distance;
      digitalWrite(trigPinFC, HIGH);
      delayMicroseconds(1000);
      digitalWrite(trigPinFC, LOW);
      duration = pulseIn(echoPinFC, HIGH);
      distance = (duration/2) / 29.1;
      return distance;
    }

  // Front left distance sensor measurement

    int distanceFL(){
      int duration, distance;
      digitalWrite(trigPinFL, HIGH);
      delayMicroseconds(1000);
      digitalWrite(trigPinFL, LOW);
      duration = pulseIn(echoPinFL, HIGH);
      distance = (duration/2) / 29.1;
      return distance;
    }


  // Front right distance sensor measurement

    int distanceFR(){
      int duration, distance;
      digitalWrite(trigPinFR, HIGH);
      delayMicroseconds(1000);
      digitalWrite(trigPinFR, LOW);
      duration = pulseIn(echoPinFR, HIGH);
      distance = (duration/2) / 29.1;
      return distance;
    }


  // Left side skirt distance measurement

    int distanceLSS(){
      int duration, distance;
      digitalWrite(trigPinLSS, HIGH);
      delayMicroseconds(1000);
      digitalWrite(trigPinLSS, LOW);
      duration = pulseIn(echoPinLSS, HIGH);
      distance = (duration/2) / 29.1;
      return distance;
    }


  // Right side skirt distance measurement

    int distanceRSS(){
      int duration, distance;
      digitalWrite(trigPinRSS, HIGH);
      delayMicroseconds(1000);
      digitalWrite(trigPinRSS, LOW);
      duration = pulseIn(echoPinRSS, HIGH);
      distance = (duration/2) / 29.1;
      return distance;
    }


  // Rear left distance measurement

    int distanceRL(){
      int duration, distance;
      digitalWrite(trigPinRL, HIGH);
      delayMicroseconds(1000);
      digitalWrite(trigPinRL, LOW);
      duration = pulseIn(echoPinRL, HIGH);
      distance = (duration/2) / 29.1;
      return distance;
    }


  // Rear right distance measurement

    int distanceRR(){
      int duration, distance;
      digitalWrite(trigPinRR, HIGH);
      delayMicroseconds(1000);
      digitalWrite(trigPinRR, LOW);
      duration = pulseIn(echoPinRR, HIGH);
      distance = (duration/2) / 29.1;
      return distance;
    }


// Movement functions

  void movement(){
    // Car will continually move forward until it meets specified parameters.
    int distance_0;
    distance_0 = distanceFC();
    while(distance_0 > 15){
      motorsOn();
      forward(1);
      distance_0 = distanceFC();
    }
    stopCar(0);
  }


  void avoidLeft(){ 
    // If the car's left side is too close to a wall, it will turn right and move forward.
    right(1500);
    }


  void avoidRight(){ 
    // If the car's right side is too close to a wall, it will turn left and move forward.
    left(1500);
    }


  void avoidBackupTurnAround(){ 
    // If the front center of the car is too close to a wall, it will drive backwards and turn around.
    backward(100);
    right(1500);
    }
    


  void avoidLeftCorner(){ 
    // If the car is stuck in a left corner, it will turn left, go backward, turn left, and go forward.
    left(1000);
    backward(100);
    left(1000);
    }


  void avoidRightCorner(){
    // If the car is stuck in a right corner, it will turn right, go backwards, turn right, and go forward.
    right(1000);
    backward(100);
    right(1000);
    }


  void avoidRightStraight(){ 
    // The car will straigthen forward when its front-left is about to be close to a wall.
    right(1000);
    forward(100);
    }


  void avoidLeftStraight(){ 
    // The car will straighten forward when its front-right is about to be close to a wall.
    left(1000);
    forward(100);
    }


  void goForward(){
    // If the car's rear end gets too close to a wall while backing up, it will move forward.
    forward(100);
  }


  void avoid(){
    // Car will move in particular directions given the parameters.
    if (distanceFC() < 8 && distanceLSS(), distanceRSS() > 10){
      avoidBackupTurnAround();
    }
    else if (distanceFL() < 7){
      avoidRightStraight();
    }
    else if (distanceFR() < 7){
      avoidLeftStraight();
    }
    else if (distanceLSS() < 7){
      avoidLeft();
    }
    else if (distanceRSS() < 7){
      avoidRight();
    }
    else if (distanceFC() < 8 && distanceLSS() < 8){
      avoidLeftCorner();
    }
    else if (distanceFC() < 8 && distanceRSS() < 8){
      avoidRightCorner();
    }
    else if (distanceRL() && distanceRR() < 8){
      goForward();
    }
}


  void leftTurnSignal() {
    // Left turn signals activates when car turns left.

      digitalWrite(frontLeftTurnSignal, HIGH);
      digitalWrite(rearLeftTurnSignal, HIGH);
      delay(100);
      digitalWrite(frontLeftTurnSignal, LOW);
      digitalWrite(rearLeftTurnSignal, LOW);
      delay(100);
      digitalWrite(frontLeftTurnSignal, HIGH);
      digitalWrite(rearLeftTurnSignal, HIGH);
      delay(100);
      digitalWrite(frontLeftTurnSignal, LOW);
      digitalWrite(rearLeftTurnSignal, LOW);
      delay(100);
      digitalWrite(frontLeftTurnSignal, HIGH);
      digitalWrite(rearLeftTurnSignal, HIGH);
      delay(100);
      digitalWrite(frontLeftTurnSignal, LOW);
      digitalWrite(rearLeftTurnSignal, LOW);
      delay(100);
      digitalWrite(frontLeftTurnSignal, HIGH);
      digitalWrite(rearLeftTurnSignal, HIGH);
      delay(100);
      digitalWrite(frontLeftTurnSignal, LOW);
      digitalWrite(rearLeftTurnSignal, LOW);
      delay(100);
      digitalWrite(frontLeftTurnSignal, HIGH);
      digitalWrite(rearLeftTurnSignal, HIGH);
      delay(100);
      digitalWrite(frontLeftTurnSignal, LOW);
      digitalWrite(rearLeftTurnSignal, LOW);
      delay(100);
      
  }


  void rightTurnSignal() {
    // Right turn signal activates when car turns right.

      digitalWrite(frontRightTurnSignal, HIGH);
      digitalWrite(rearRightTurnSignal, HIGH);
      delay(100);
      digitalWrite(frontRightTurnSignal, LOW);
      digitalWrite(rearRightTurnSignal, LOW);
      delay(100);
      digitalWrite(frontRightTurnSignal, HIGH);
      digitalWrite(rearRightTurnSignal, HIGH);
      delay(100);
      digitalWrite(frontRightTurnSignal, LOW);
      digitalWrite(rearRightTurnSignal, LOW);
      delay(100);
      digitalWrite(frontRightTurnSignal, HIGH);
      digitalWrite(rearRightTurnSignal, HIGH);
      delay(100);
      digitalWrite(frontRightTurnSignal, LOW);
      digitalWrite(rearRightTurnSignal, LOW);
      delay(100);
      digitalWrite(frontRightTurnSignal, HIGH);
      digitalWrite(rearRightTurnSignal, HIGH);
      delay(100);
      digitalWrite(frontRightTurnSignal, LOW);
      digitalWrite(rearRightTurnSignal, LOW);
      delay(100);
      digitalWrite(frontRightTurnSignal, HIGH);
      digitalWrite(rearRightTurnSignal, HIGH);
      delay(100);
      digitalWrite(frontRightTurnSignal, LOW);
      digitalWrite(rearRightTurnSignal, LOW);
      delay(100);

  }

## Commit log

2021-05-18 05/17/2021 Update
    [9Vbattery.SLDPRT, 9VbatteryBracket.SLDPRT, 9VbatteryBracket.STL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]
2021-10-28 10/27/2021 Update
    SolidWorks drawing implementation begins.
    [9VbatteryBracket.SLDDRW, 9VbatteryBracket.SLDPRT, AAbatteryPackBracket.SLDDRW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]
2021-12-12 12/12/2021 Update
    All engineering drawings for the originally designed mechanical parts are complete.
    [bottomChassis.SLDDRW, bottomChassis.SLDPRT, frontBumperToTopHeadLightBracket.SLDPRT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]
2021-12-23 12/22/2021 Update
    Instruction booklet text started.
    [L298NmotorDriver.SLDPRT, M2.5mmNut.SLDPRT, M2.5mmx12mmHexCap.SLDPRT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]
2021-12-23 12/23/2021
    Progress has been made to the rough draft of the instruction booklet text.
    [M4mmx12mmPhillipsHead.SLDPRT, usbTypeAtoUsbTypeAcable.SLDPRT]
2021-12-24 12/23/2021 Update
    Updates to the rough draft of the instruction booklet text where it now exceeds 120 steps.
    [M2.5mmx16mmHexCap.SLDPRT, M2.5mmx74.5mmStandOffScrew.SLDPRT, M2.5mmx8mmHexCap.SLDPRT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]
2021-12-26 12/25/2021
    Written procedure on how to fabricate the headlights is complete. Working on writing a procedure on how to install them.
    [M2.5mmx20mmHexCap.SLDPRT, M2.5mmx30mmHexCap.SLDPRT, clearLED.SLDPRT]
2021-12-26 12/26/2021 Update
    Procedure on how to fasten the headlights to the front bumper and electronically connect them to the Arduino has been completed. Procedure on how to fasten the front bumper to the bottom chassis in p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
2021-12-27 12/26/2021 Update
    Procedure on how to fabricate the toggle switch AA battery pack assembly has been completed. Next is to write a procedure on how to fabricate the 9V battery toggle switch assembly.
2021-12-27 12/27/2021
    Written procedure on how to assemble the vrsLearningKit including fabrication is now complete (rough draft). Some ideas will be explored before visual illustrations are made. Inspiration may come fro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
    [9Vbattery.SLDPRT, AAbatteryPack.SLDPRT, sideShell.SLDDRW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]
2021-12-31 12/30/2021 Update
    The exploded view of the entire assembly is complete.
    [M2.5mmx12mmHexCap.SLDPRT, M2.5mmx16mmHexCap.SLDPRT, M2.5mmx18mmHexCap.SLDPRT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]
2021-12-31 12/30/2021 Update
    Visual illustration addition has started.
    [toggle_mts1_assembly.SLDASM]
2022-04-09 04/09/2022 Update
    Completed steps 1-12 on the instruction booklet.
    [Step 1.SLDASM, Step 3.SLDASM, Step 4.SLDASM]
2022-09-17 09/17/2022 Final Update
    [9VbatteryBracket.SLDDRW, AAbatteryPackBracket.SLDPRT, Step 1.SLDASM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]
